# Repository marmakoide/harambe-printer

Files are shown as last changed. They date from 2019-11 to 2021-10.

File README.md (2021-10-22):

# Harambe printer

This repository contains the design of a 3d printer. The printer is very 
similar to a Prusa MK3 with the Bear upgrade. The differences are

* 12mm smooth rods on Z and Y axis for extra rigidity
* 9mm belts on all axes
* Duet2 for control
* Cast aluminium bed with silicon 220V heater
* Self-aligning linear bearings on Z and Y axis

The target I am aiming for is a very reliable, easy to service 3d printer. 

I designed all the 3d printed parts as an exercise to learn 3d modeling and 
mecanical design.

## Authors

* **Alexandre Devert** - *Initial work* - [marmakoide](https://github.com/marmakoide)

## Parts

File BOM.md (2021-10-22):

Bill Of Materials
=================

* Prusa i3 Bear MK3 frame kit
* Filafarm Filabase  218x218 mm 230V/200W heated bed kit
* 2x 12mm smooth rods, length 370 mm
* 2x Nema17 steppers with integrated TR8x8 leadscrew
* 2x TR8x8 leadscrew bronze nuts
* 4x LM12UU linear ball bearings (European specs, 12x22x32 mmm)
* 2x Topball TK12 self-aligning linear ball bearings
* 3x Gates Powergrip® 2GT Toothed Idler 9mm Belt, 20 Teeths
* 1x LRS-350-24, 24V 350 Watts switching power supply
* 1x Duet 2 Wifi control board
* 1x Panel Due touch screen module

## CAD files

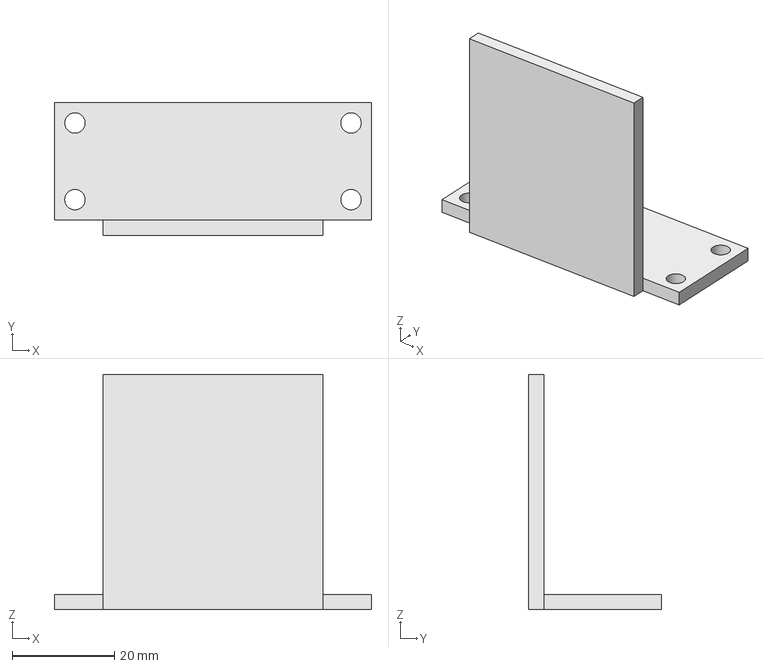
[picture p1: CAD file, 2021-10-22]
parts.FCStd
62.0 x 26.0 x 46.0 mm

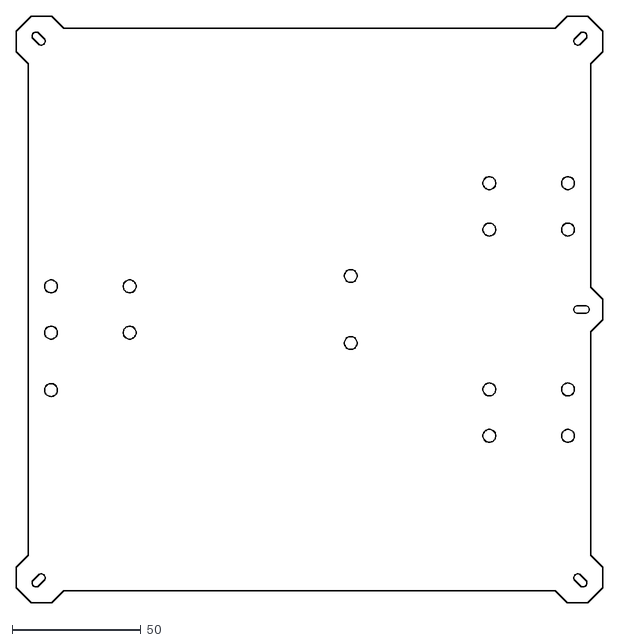
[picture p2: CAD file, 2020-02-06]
parts/dxf/bed-support-plate.dxf
227.3 x 227.3

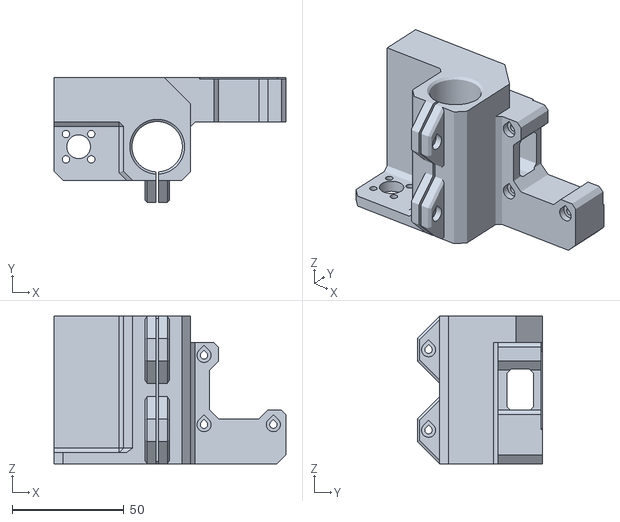
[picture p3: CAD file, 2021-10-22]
parts/stl/x-motor-mount.stl
103.8 x 56.0 x 66.0

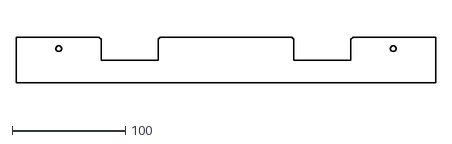
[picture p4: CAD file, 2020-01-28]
parts/dxf/y-axis-fitting-jig-a.dxf
370.0 x 40.0

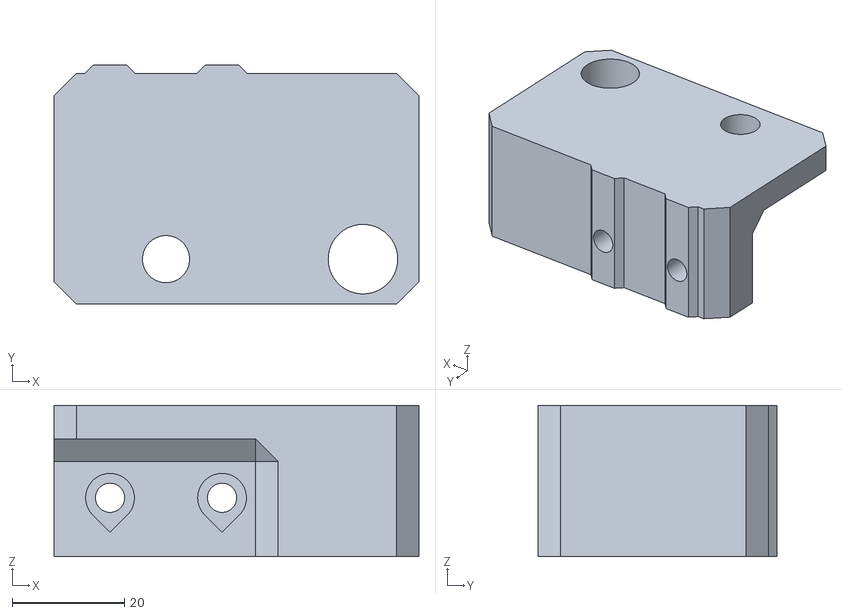
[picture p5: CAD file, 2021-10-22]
parts/stl/z-top.stl
65.2 x 42.7 x 27.0

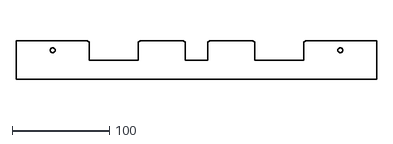
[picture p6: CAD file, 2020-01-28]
parts/dxf/y-axis-fitting-jig-b.dxf
370.0 x 40.0

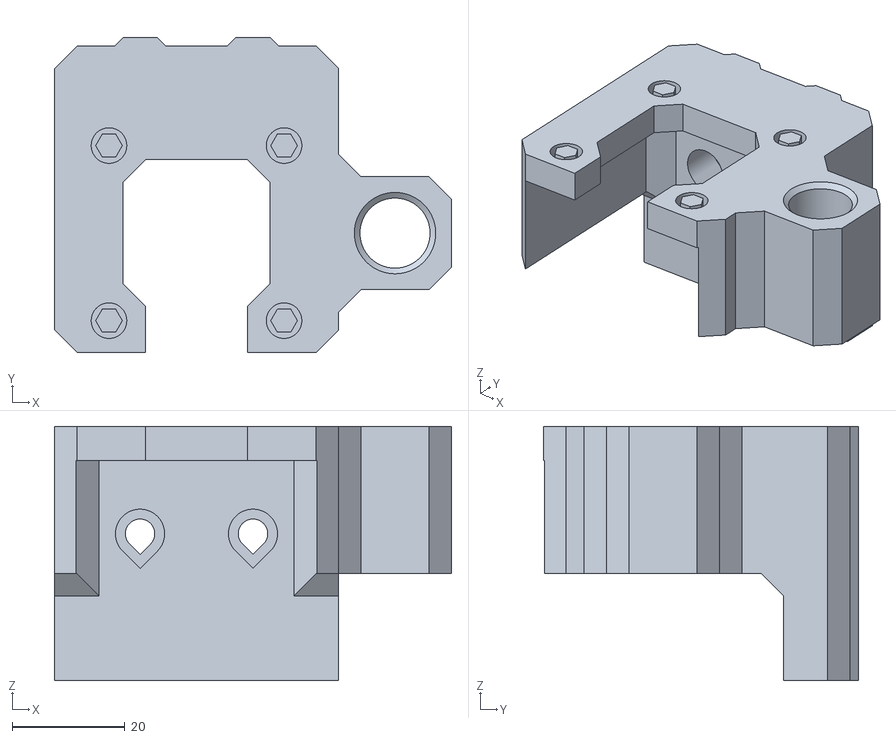
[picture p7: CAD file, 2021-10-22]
parts/stl/z-motor-mount.stl
70.3 x 55.8 x 45.0

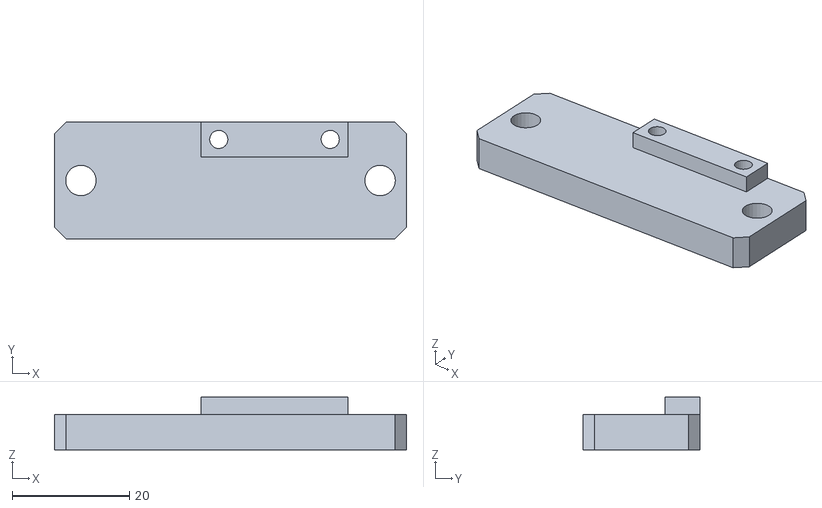
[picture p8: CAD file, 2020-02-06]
parts/stl/y-endstop-support.stl
60.0 x 20.0 x 9.00

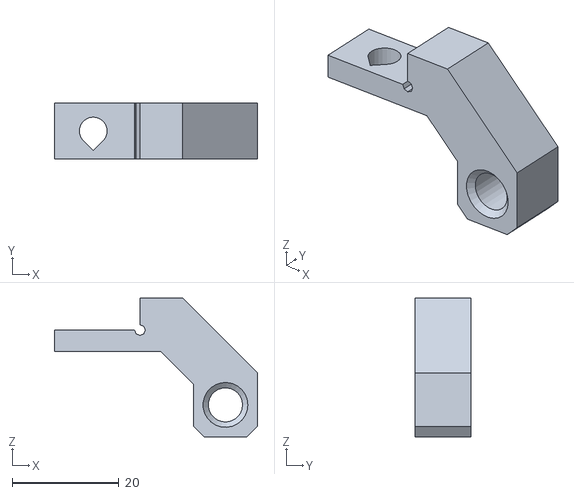
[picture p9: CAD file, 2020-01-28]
parts/stl/y-endstop-hammer-support.stl
38.0 x 10.5 x 26.0

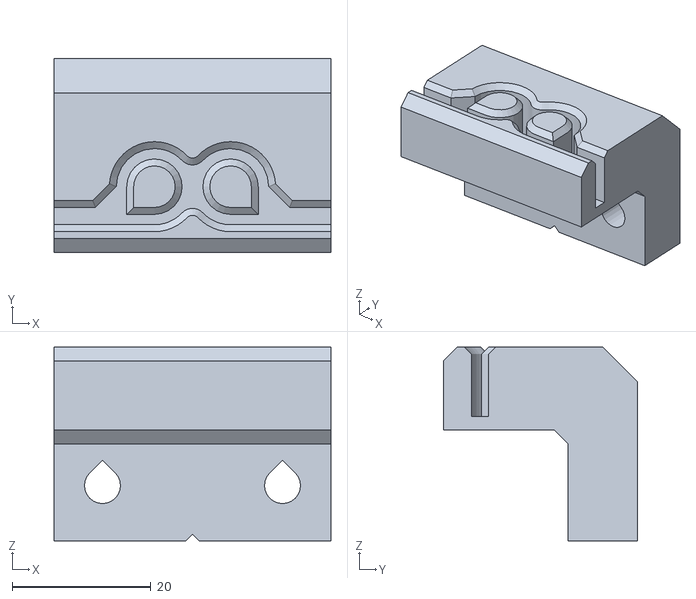
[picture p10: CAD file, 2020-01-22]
parts/stl/y-belt-clamp.stl
40.0 x 28.0 x 28.0

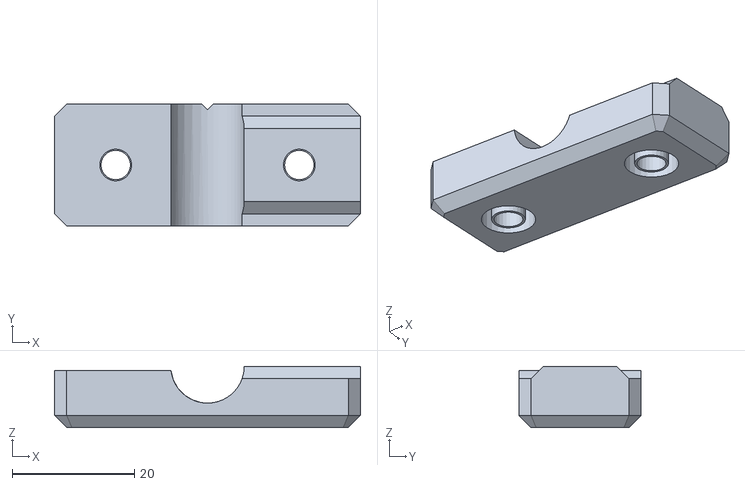
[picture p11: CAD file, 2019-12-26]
parts/stl/y-rod-holder-top.stl
50.0 x 20.0 x 10.0

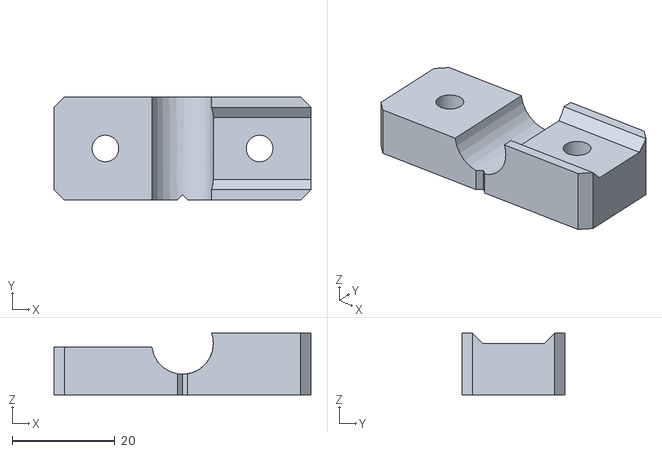
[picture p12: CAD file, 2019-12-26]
parts/stl/y-rod-holder-bottom.stl
50.0 x 20.0 x 12.0

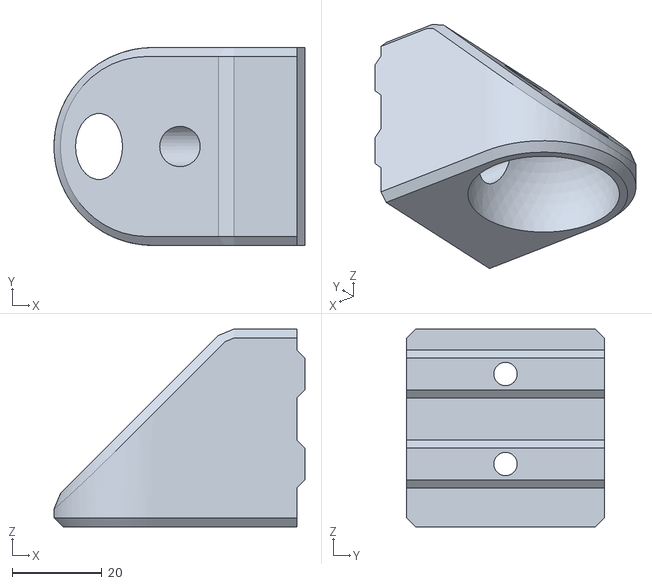
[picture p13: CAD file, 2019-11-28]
parts/stl/foot.stl
55.8 x 44.0 x 44.0

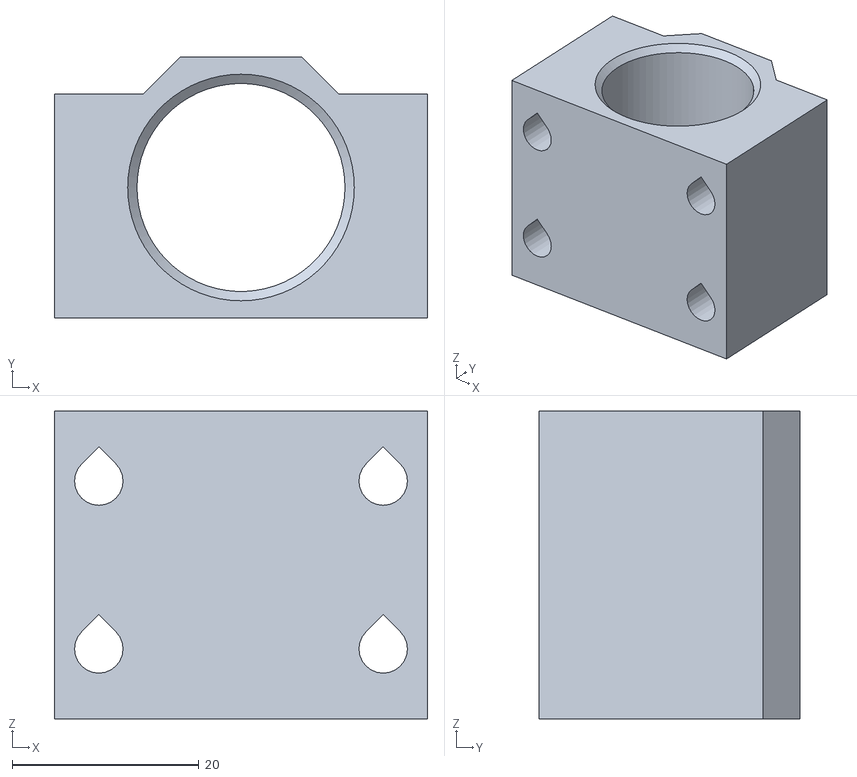
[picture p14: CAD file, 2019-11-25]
parts/stl/y-bearing-holder-type-a.stl
40.0 x 28.0 x 33.0

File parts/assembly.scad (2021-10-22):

include <parts.scad>

X_AXIS_POS = 0 - BED_SIZE / 2;
Y_AXIS_POS = BED_SIZE / 2; //BED_SIZE - 9;
Z_AXIS_POS = 0;



/*
 * Prefab parts
 */

module bmg_extruder() {
  CUBE_SIZE = [42, 33, 33];
  
  HEATBREAK_HEIGHT = 6;
  HEATBREAK_DIAMETER = 5.88;

  
  // Body (upper part is not represented)
  hull() {
    cube(CUBE_SIZE, center = true);
    rotate(90, [0, 0, 1])
      cube(CUBE_SIZE, center = true);
  }
  
  // Bottom part of the heatbreak
  translate([-(CUBE_SIZE[0] + HEATBREAK_HEIGHT) / 2, 4.25, 23 - CUBE_SIZE[0] / 2]) {
    // Bottom part of the heatbreak
    rotate(90, [0, 1, 0])
      kcylinder(HEATBREAK_DIAMETER / 2, HEATBREAK_HEIGHT);
    
    // Heatblock
    translate([-3 - 11.5 / 2 + 6 - 2, 0, 0])
    rotate(90, [0, 1, 0])
    translate([E3D_V6_HEATBLOCK_SIZE_FILAMENT_PATH_OFFSET / 2, 0, 0])
    difference() {
      cube(E3D_V6_HEATBLOCK_SIZE, center = true);
      translate([E3D_V6_HEATBLOCK_SIZE_FILAMENT_PATH_OFFSET - E3D_V6_HEATBLOCK_SIZE[0] / 2, 0, 0])
      kcylinder(3, E3D_V6_HEATBLOCK_SIZE[2] + 2);
    }
  }
}



module nema17(length) {
  CUBE_SIZE = [NEMA_17_SIZE, 33, length];
  
  SHAFT_DIAMETER = 5;
  SHAFT_LENGTH = 24;
  
  FLANGE_DIAMETER = 22;
  FLANGE_HEIGHT = 2;
  
  FIXATION_HOLES_DIAMETER = 3.5;
  FIXATION_HOLES_GAP = 31; 
  FIXATION_HOLES_DEPTH = 15;

  cyl_resolution = 16;
  
  difference() {
    union() {
      // Main body
      color("DarkSlateGray")
        hull() {
          cube(CUBE_SIZE, center = true);
          rotate(90, [0, 0, 1])
            cube(CUBE_SIZE, center = true);
         }

      // Flange
      color(METAL_COLOR)
        translate([0, 0, (CUBE_SIZE[2] / 2) - 1])
          cylinder(h = FLANGE_HEIGHT + 1, d = FLANGE_DIAMETER, center = true, $fn = cyl_resolution);
      
      // Shaft
      color(METAL_COLOR)
        translate([0, 0, (CUBE_SIZE[2] + SHAFT_LENGTH) / 2])
          cylinder(h = SHAFT_LENGTH, d = SHAFT_DIAMETER, center = true, $fn = cyl_resolution);
    }

    // Fixation holes
    //color("DarkSlateGray")
    translate([0, 0, (CUBE_SIZE[2] / 2) - (FIXATION_HOLES_DEPTH / 2) + 1])
      for(i = [-.5, .5], j = [-.5, .5])
        translate([i * FIXATION_HOLES_GAP, j * FIXATION_HOLES_GAP, 0])
          cylinder(h = FIXATION_HOLES_DEPTH + 1, d = FIXATION_HOLES_DIAMETER, center = true, $fn = cyl_resolution);
  }
}




/*
 * Gantry parts
 */

module beam(length) {
  color(BEAM_COLOR)
    vslot_beam(length);
}

module x_beam() {
  rotate(90, [1, 0, 0])
    beam(X_BEAM_SIZE);
}

module y_beam() {
  rotate(90, [0, 0, 1])
    beam(Y_BEAM_SIZE);
}

module z_beam() {
  rotate(90, [0, 0, 1])
  rotate(90, [0, 1, 0])
    beam(Z_BEAM_SIZE);
}

module zx_beam() {
  rotate(90, [1, 0, 0])
    beam(ZX_BEAM_SIZE);
}



/*
 * X axis parts
 */

module x_rod() {
  color(METAL_COLOR)
    rotate(90, [0, 1, 0])
      kcylinder(X_ROD_DIAMETER / 2, X_ROD_LENGTH);
}

module x_bearing_block_() {
  color(PRINTED_PART_COLOR)
    rotate(90, [0, 1, 0])
    rotate(180, [1, 0, 0])
      x_bearing_block();
}

module x_axis_carriage_assembly() {
  // extruder mount plate
  translate([0, X_BEARING_BLOCK_SIZE[1] / 2 + BONDTECH_BMG_MOUNT_SHEET_THICKNESS / 2, 0])
    rotate(180, [0, 1, 0])
    rotate(-90, [1, 0, 0])
    bondtech_bmg_mount();

  // extruder stepper motor
  translate([0, X_BEARING_BLOCK_SIZE[1] / 2 + 43 / 2 + BONDTECH_BMG_MOUNT_SHEET_THICKNESS, 0])
    rotate(180, [0, 1, 0])
    rotate(-90, [0, 1, 0])
      nema17(E_NEMA_17_HEIGHT);
  
  // extruder
  translate([31, X_BEARING_BLOCK_SIZE[1] / 2 + 43 / 2 + BONDTECH_BMG_MOUNT_SHEET_THICKNESS, 0])
    rotate(180, [0, 1, 0])
    rotate(90, [0, 1, 0])  
      bmg_extruder();
  
  // bearing blocks
  translate([-X_BEARING_BLOCK_SIZE[2] / 2, 0, X_ROD_GAP / 2])
    x_bearing_block_();
  
  translate([ X_BEARING_BLOCK_SIZE[2] / 2, 0, X_ROD_GAP / 2])
    x_bearing_block_();
  
  translate([0, 0, -X_ROD_GAP / 2])
    x_bearing_block_();  
}

module x_axis_assembly() {
  // bearing blocks
  translate([X_AXIS_POS, 0, 0])
    x_axis_carriage_assembly();
  
  // X rods
  translate([0, 0, -X_ROD_GAP / 2])
    x_rod();
  
  translate([0, 0, X_ROD_GAP / 2])
    x_rod();  
}



/*
 * Y axis parts
 */

module y_rod() {
  color(METAL_COLOR)
    rotate(90, [1, 0, 0])
      kcylinder(Y_ROD_DIAMETER / 2, Y_ROD_LENGTH);
}

module y_bearing_block_() {
  color(PRINTED_PART_COLOR)
    rotate(90, [1, 0, 0])
    rotate(180, [0, 0, 1])
      render(convexity = 2)
      y_bearing_block();
}

module y_end_stop_support() {
  color(PRINTED_PART_COLOR)
    import("./stl/y-endstop-support.stl", convexity = 3);
}

module y_end_stop_hammer_support() {
  color(PRINTED_PART_COLOR)
    rotate(180, [0, 0, 1])
    import("./stl/y-endstop-hammer-support.stl", convexity = 3);
}

module y_belt_clamp() {
  color(PRINTED_PART_COLOR)
    translate([0, -Y_BELT_CLAMP_SIZE[0] / 2, 0])
    rotate(90, [0, 0, 1])
    rotate(90, [1, 0, 0])
      import("./stl/y-belt-clamp.stl", convexity = 3);
}

module y_motor_mount() {
  color(PRINTED_PART_COLOR)
    rotate(90, [0, 0, 1])
    rotate(90, [1, 0, 0])
      import("./stl/y-motor-mount.stl", convexity = 3);
}

module y_pulley_idler() {
  color(PRINTED_PART_COLOR)
    rotate(180, [0, 1, 0])
    rotate(90, [0, 0, -1])
      import("./stl/y-pulley-idler.stl");
}

module y_pulley_idler_assembly() {
  y_pulley_idler();
  
  translate([0, -18.25, 15 - 21.15])
  rotate(90, [0, 1, 0])
    gates_toothed_idler_9mm();
}

module y_motor_assembly() {
  y_motor_mount();
  
  translate([-(XYZ_NEMA_17_HEIGHT + Y_MOTOR_MOUNT_WIDTH) / 2, NEMA_17_SIZE / 2 + 4, -6.15])
  rotate(90, [0, 1, 0])
    nema17(XYZ_NEMA_17_HEIGHT);
}



module y_axis_assembly() {
  translate([0, -Y_BEAM_SIZE / 2, 0])
    y_motor_assembly();
  
  translate([0,  Y_BEAM_SIZE / 2, 0])
    y_pulley_idler_assembly();
  
  translate([-Y_ROD_GAP / 2 - 50, -Y_BEAM_SIZE / 2 - 10, 0])
    y_end_stop_support();
  
  // Belt
  translate([0, 0, 15 - 21.15])
  rotate(90, [0, 0, 1])
  rotate(90, [1, 0, 0])
    belt(Y_BEAM_SIZE - 40, GATES_TOOTHED_IDLER_OUTER_DIAMETER, 9);

  // Y rods
  translate([0, 0, Y_ROD_DIAMETER / 2 + 4]) {
    translate([-Y_ROD_GAP / 2, 0, 0])
      y_rod();
  
    translate([ Y_ROD_GAP / 2, 0, 0])
      y_rod();
  }  
}



/*
 * Z axis parts
 */

module z_rod() {
  color(METAL_COLOR)
    kcylinder(Z_ROD_DIAMETER / 2, Z_ROD_LENGTH);
}

module z_axis_assembly() {
  // Z rods
  //translate([0, 0, Y_ROD_DIAMETER / 2 + 4]) {
    translate([-Z_ROD_GAP / 2, 0, Z_ROD_LENGTH / 2])
      z_rod();
  
    translate([ Z_ROD_GAP / 2, 0, Z_ROD_LENGTH / 2])
      z_rod();
  //}  
}



/*
 * Bed parts
 */

module bed_support_plate() {
  color("Burlywood")
    linear_extrude(height = BED_SUPPORT_THICKNESS, convexity = 10, center = true)
      bed_support_plate_profile();  
}

module bed_assembly() {
   A = (Y_BEARING_BLOCK_SIZE[1] + Y_BEARING_BLOCK_BEVEL) / 2;
  
  // bed support plate
  translate([0, 0, BED_SUPPORT_THICKNESS / 2 + Y_BEARING_BLOCK_SIZE[1] / 2])
    bed_support_plate();
  
  // belt clamps
  translate([10, 0, 0])
   rotate(180, [0, 0, 1])
    translate([0, 0, 0])
    y_belt_clamp();
  
  // end stop hammer
  translate([-(BED_SIZE / 2 - 16), -(BED_SIZE / 4 - A) - Y_BEARING_BLOCK_SIZE[2] / 2 + Y_ENDSTOP_HAMMER_THICKNESS / 2 + 20, BED_SUPPORT_THICKNESS / 2 + Y_BEARING_BLOCK_SIZE[1] / 2 + BED_SUPPORT_THICKNESS / 2])
    y_end_stop_hammer_support();

  // bearing blocks 
  translate([-Y_ROD_GAP / 2, 0, 0]) {
    translate([0, Y_BEARING_BLOCK_BEVEL / 2, 0])
    rotate(90, [1, 0, 0])
      lm12uue();

    y_bearing_block_();
  }
  
  translate([ Y_ROD_GAP / 2, -(BED_SIZE / 4 - A), 0]) {
    translate([0, Y_BEARING_BLOCK_BEVEL / 2, 0])
    rotate(90, [1, 0, 0])
      lm12uue();
    
    y_bearing_block_();
  }
  
  translate([ Y_ROD_GAP / 2, (BED_SIZE / 4 - A), 0]) {
    translate([0, Y_BEARING_BLOCK_BEVEL / 2, 0])
    rotate(90, [1, 0, 0])
      lm12uue();

    y_bearing_block_();
  }
}



/*
 * Overall assembly
 */

module gantry_assembly() {
  translate([0, -(Y_BEAM_SIZE / 2 + 10), 20])
    x_beam();
  translate([0,  (Y_BEAM_SIZE / 2 + 10), 20])
    x_beam();
  translate([-(Y_BEAM_SIZE / 2), 0, 10])
    y_beam();  
  translate([ (Y_BEAM_SIZE / 2), 0, 10])
    y_beam();
  translate([-(X_BEAM_SIZE / 2 - 20), 0, Z_BEAM_SIZE / 2 + 20]) 
    z_beam();
  translate([ (X_BEAM_SIZE / 2 - 20), 0, Z_BEAM_SIZE / 2 + 20]) 
    z_beam();
  translate([0, 0, Z_BEAM_SIZE])   
    zx_beam();
}



module printer_assembly() {
  // gantry
  gantry_assembly();
  
  // bed
  translate([0, Y_AXIS_POS - BED_SIZE / 2, 40 + 6 + 4])
    bed_assembly();
  
  // x axis
  translate([0, 30, 40 + X_ROD_GAP + 40])
    x_axis_assembly();
  
  // y axis
  translate([0, 0, 40])  
    y_axis_assembly();
  
  // z axis
  translate([0, Z_ROD_DIAMETER / 2 + 10, 20])  
    z_axis_assembly();
}

printer_assembly();

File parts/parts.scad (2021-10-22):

include <utils.scad>



// --- Parameters ------------------------------------------------------------

BEAM_COLOR = "SlateGray";
PRINTED_PART_COLOR = "Orange";
METAL_COLOR = "Gainsboro";
BELT_COLOR = "Black";

X_BEAM_SIZE  = 370;
Y_BEAM_SIZE  = 331;
Z_BEAM_SIZE  = 359; 
ZX_BEAM_SIZE = 290; 

// Nema17 stepper motor specs
NEMA_17_SIZE = 42.3;
XYZ_NEMA_17_HEIGHT = 39.8;
E_NEMA_17_HEIGHT = 23;

// Gates pulleys specs
GATES_TOOTHED_IDLER_OUTER_DIAMETER = 15;

// E3D V6 heatblock
E3D_V6_HEATBLOCK_SIZE = [23, 16, 11.5];
E3D_V6_HEATBLOCK_SIZE_FILAMENT_PATH_OFFSET = 8;

// LM8UUE bearing specs
LM8UUE_L = 25;
LM8UUE_D = 16;

// LM12UUE bearing specs
LM12UUE_L = 32;
LM12UUE_D = 22;

// Extruder elements
BONDTECH_BMG_MOUNT_PLATE_SIZE = [23, 62];
BONDTECH_BMG_MOUNT_SHEET_THICKNESS = 3;
BONDTECH_BMG_MOUNT_HOLE_DIAMETER = 4;

// X axis design
X_ROD_DIAMETER = 8;
X_ROD_LENGTH = 500;
X_ROD_GAP = 50;

// Y axis design
Y_ROD_DIAMETER = 12;
Y_ROD_LENGTH = Y_BEAM_SIZE + 40;
Y_ROD_GAP = 170;

// Z axis design
Z_ROD_DIAMETER = 12;
Z_ROD_LENGTH = Z_BEAM_SIZE;
Z_ROD_GAP = X_BEAM_SIZE - 20; 

// Y rod holders
Y_ROD_HOLDER_SIZE = [50, 40, 2 * 4 + Y_ROD_DIAMETER];

// Y belt clamp
Y_BELT_CLAMP_SIZE = [40, 28, 28];
Y_BELT_CLAMP_FIXATION_HOLE_GAP = 26;

// Y end stop hammer
Y_ENDSTOP_HAMMER_THICKNESS = 10.5;

// Y motor mount
Y_MOTOR_MOUNT_WIDTH = 23;
Y_MOTOR_MOUNT_MOTOR_BEAM_GAP = 4;

// X bearing blocks
X_BEARING_LENGTH = LM8UUE_L;
X_BEARING_DIAMETER = LM8UUE_D;
X_BEARING_BLOCK_BEVEL = 1;
X_BEARING_BLOCK_SIZE = [34, 22, X_BEARING_LENGTH + X_BEARING_BLOCK_BEVEL];
X_BEARING_BLOCK_FIXATION_HOLE_GAP_X = 24;
X_BEARING_BLOCK_FIXATION_HOLE_GAP_Y = 13;

// Y bearing blocks
Y_BEARING_LENGTH = LM12UUE_L;
Y_BEARING_DIAMETER = LM12UUE_D;
Y_BEARING_BLOCK_BEVEL = 1;
Y_BEARING_BLOCK_SIZE = [40, 28, Y_BEARING_LENGTH + Y_BEARING_BLOCK_BEVEL];
Y_BEARING_BLOCK_FIXATION_HOLE_GAP_X = 30.5;
Y_BEARING_BLOCK_FIXATION_HOLE_GAP_Y = 18;

// Y axis fitting jigs 
Y_AXIS_FITTING_JIG_TOLERANCE = .2;
Y_AXIS_FITTING_JIG_CHAMFER = 2;

BED_SIZE = 218;

BED_SUPPORT_ADJUSTEMENT_SCREW_GAP = 5;
BED_SUPPORT_ADJUSTEMENT_SCREW_SLOT_LENGTH = 3;
BED_SUPPORT_THICKNESS = 6;

M3_LASER_CUT_HOLE_DIAMETER = 3.;

M4_LASER_CUT_HOLE_DIAMETER = 4.;

M5_3D_PRINT_HOLE_DIAMETER = 5.2;
M5_LASER_CUT_HOLE_DIAMETER = 5.;


// --- Utilities -------------------------------------------------------------

// Circumradius of an octagon with size 1
octagon_circumradius = (sqrt(4 + 2 * sqrt(2))) / 2;

module k_negative_rectangle(size, chamfer) {
  square(size, center = true);
  polygon([
            [-(size[0] / 2 + chamfer), size[1] / 2],
            [  size[0] / 2 + chamfer,  size[1] / 2],
            [  size[0] / 2,            size[1] / 2 - chamfer],
            [ -size[0] / 2,            size[1] / 2 - chamfer]
          ], convexity = 1);
}



// --- Commonly used elements -------------------------------------------------

module m4_teardrop_3d_print() {
  kteardrop(M4_LASER_CUT_HOLE_DIAMETER / 2);
}

module m5_teardrop_3d_print() {
  kteardrop(M5_LASER_CUT_HOLE_DIAMETER / 2);
}

module m3_circle_laser_cut() {
  kcircle(M3_LASER_CUT_HOLE_DIAMETER / 2);
}

module m5_circle_laser_cut() {
  kcircle(M5_LASER_CUT_HOLE_DIAMETER / 2);
}



// --- GT2 belt ----------------------------------------------------------------------------------

module belt(length, diameter, width) {
  THICKNESS = 0.63;
  
  color(BELT_COLOR)
    linear_extrude(height = width, center = true)
      difference() {
        kcapsule(length, diameter / 2 + THICKNESS);
        kcapsule(length, diameter / 2);
      }
}



// --- Linear bearings ---------------------------------------------------------------------------

module lm12uue() {
  color(METAL_COLOR)
    difference() {
      kcylinder(LM12UUE_D / 2, LM12UUE_L);
      kcylinder(6, LM12UUE_L + 2);
    }
}



module lm8uue() {
  color(METAL_COLOR)
    difference() {
      kcylinder(LM8UUE_D / 2, LM8UUE_L);
      kcylinder(4, LM8UUE_L + 2);
    }
}



// --- Gates pulley idler for 9mm 2GT belts ------------------------------------------------------

module gates_toothed_idler_9mm() {
  HOLE_DIAMETER = 5;
  INNER_DIAMETER = 12.22;
  OUTER_DIAMETER = GATES_TOOTHED_IDLER_OUTER_DIAMETER;
  LENGTH = 14;
  BORDER_SIZE = 1.5;
  
  color(METAL_COLOR) {
    difference() {
      union() {
        kcylinder(INNER_DIAMETER / 2, LENGTH);
      
        translate([0, 0, (LENGTH - BORDER_SIZE) / 2])
          kcylinder(OUTER_DIAMETER / 2, BORDER_SIZE);
        
        translate([0, 0, -(LENGTH - BORDER_SIZE) / 2])
          kcylinder(OUTER_DIAMETER / 2, BORDER_SIZE);
      }
      
      kcylinder(HOLE_DIAMETER / 2, 16.);      
    }
  }
}



// --- Bondtech BMG extruder mount ---------------------------------------------------------------

module bondtech_bmg_mount() {
  color(METAL_COLOR) {
    linear_extrude(height = BONDTECH_BMG_MOUNT_SHEET_THICKNESS, center = true) {
      difference() {
        square(BONDTECH_BMG_MOUNT_PLATE_SIZE, center = true);
        translate([-15 / 2, -55 / 2])
          kcircle(BONDTECH_BMG_MOUNT_HOLE_DIAMETER / 2);
        translate([ 15 / 2, -55 / 2])
          kcircle(BONDTECH_BMG_MOUNT_HOLE_DIAMETER / 2);
        translate([-15 / 2,  55 / 2])
          kcircle(BONDTECH_BMG_MOUNT_HOLE_DIAMETER / 2);
        translate([ 15 / 2,  55 / 2])
          kcircle(BONDTECH_BMG_MOUNT_HOLE_DIAMETER / 2);
      }
    }
    
    translate([-(BONDTECH_BMG_MOUNT_PLATE_SIZE[0] + BONDTECH_BMG_MOUNT_SHEET_THICKNESS) / 2, 0, 43 / 2 + BONDTECH_BMG_MOUNT_SHEET_THICKNESS])
    rotate(90, [1, 0, 0])
    rotate(90, [0, 1, 0])
    linear_extrude(height = BONDTECH_BMG_MOUNT_SHEET_THICKNESS, center = true) {
      difference() {
        translate([0, -BONDTECH_BMG_MOUNT_SHEET_THICKNESS])
          square([43, 46], center = true);
        
        translate([0, -BONDTECH_BMG_MOUNT_SHEET_THICKNESS / 2]) {
          kcircle(23 / 2);
        
          translate([-31 / 2, -31 / 2])
            kcircle(BONDTECH_BMG_MOUNT_HOLE_DIAMETER / 2);
          translate([ 31 / 2, -31 / 2])
            kcircle(BONDTECH_BMG_MOUNT_HOLE_DIAMETER / 2);
          translate([-31 / 2,  31 / 2])
            kcircle(BONDTECH_BMG_MOUNT_HOLE_DIAMETER / 2);
          translate([ 31 / 2,  31 / 2])
            kcircle(BONDTECH_BMG_MOUNT_HOLE_DIAMETER / 2);
        }
      }
    }
  }
}



// --- X bearing block --------------------------------------------------------

module x_bearing_block() {
  FLAT_HEIGHT = 3;
  A = X_BEARING_BLOCK_SIZE[0] - X_BEARING_BLOCK_FIXATION_HOLE_GAP_X;
  
  BEARING_BLOCK_FIXATION_HOLE_POS_LIST = [
    [-X_BEARING_BLOCK_FIXATION_HOLE_GAP_X, 0, -X_BEARING_BLOCK_FIXATION_HOLE_GAP_Y],
    [ X_BEARING_BLOCK_FIXATION_HOLE_GAP_X, 0, -X_BEARING_BLOCK_FIXATION_HOLE_GAP_Y],
    [-X_BEARING_BLOCK_FIXATION_HOLE_GAP_X, 0,  X_BEARING_BLOCK_FIXATION_HOLE_GAP_Y],
    [ X_BEARING_BLOCK_FIXATION_HOLE_GAP_X, 0,  X_BEARING_BLOCK_FIXATION_HOLE_GAP_Y]
  ] / 2;
  
  difference() {
    // Main shape
    linear_extrude(height = X_BEARING_BLOCK_SIZE[2], convexity = 2, center = true)
      difference() {
        // Bearing hole profile
        polygon([
          [ X_BEARING_BLOCK_SIZE[0] / 2, -X_BEARING_BLOCK_SIZE[1] / 2],
          [ X_BEARING_BLOCK_SIZE[0] / 2,  X_BEARING_BLOCK_SIZE[1] / 2 - FLAT_HEIGHT],
          [ X_BEARING_BLOCK_SIZE[0] / 2 - A,  X_BEARING_BLOCK_SIZE[1] / 2 - FLAT_HEIGHT],
          [ X_BEARING_BLOCK_SIZE[0] / 2 - A - FLAT_HEIGHT,  X_BEARING_BLOCK_SIZE[1] / 2],
          [-X_BEARING_BLOCK_SIZE[0] / 2 + A + FLAT_HEIGHT,  X_BEARING_BLOCK_SIZE[1] / 2], 
          [-X_BEARING_BLOCK_SIZE[0] / 2 + A,  X_BEARING_BLOCK_SIZE[1] / 2 - FLAT_HEIGHT],
          [-X_BEARING_BLOCK_SIZE[0] / 2,  X_BEARING_BLOCK_SIZE[1] / 2 - FLAT_HEIGHT],
          [-X_BEARING_BLOCK_SIZE[0] / 2, -X_BEARING_BLOCK_SIZE[1] / 2],        
        ], convexity = 1);
      
        // Bearing hole
        kcircle(X_BEARING_DIAMETER / 2);
      }
      
    // Fixation holes
    for(pos = BEARING_BLOCK_FIXATION_HOLE_POS_LIST)
      translate(pos)
        rotate(90, [1, 0, 0])
          linear_extrude(height = 2 * X_BEARING_BLOCK_SIZE[1], convexity = 1, center = true)
            rotate(90)
              m4_teardrop_3d_print();
    
    // Bearing hole bevel
    translate([0, 0, X_BEARING_BLOCK_SIZE[2] / 2])
      round_hole_bevel(X_BEARING_DIAMETER / 2, X_BEARING_BLOCK_BEVEL, [0, 0, 1]);    
  }  
}

//x_bearing_block();



// --- Y bearing block --------------------------------------------------------
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

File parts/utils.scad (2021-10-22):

CHORD_LEN = .4; // Length of segments used to approximate curves


function mirror_x(U) =
  [-U[0], U[1]];



/*
 * Euclidean norm and distance
 */
 
function norm2(v) =
  sqrt(v * v);

function dist(A, B) =
	norm2([B[0] - A[0], B[1] - A[1]]);
  
  

/*
 * Rotate an object so that U aligns to V
 */
 
module align_to_axis(U, V) {
  rotate(acos(U * V), cross(U, V))
    children(0);
}



/*
 * Produce n evenly spaced values in [a, b] interval
 */
 
function linspace(a, b, n) =
  [ for (_i = [ 0 : n - 1 ] ) a + _i * (b - a) / (n - 1) ];
  
function linspace_noend(a, b, n) =
  [ for (_i = [ 0 : n - 1 ] ) a + _i * (b - a) / n ];




function chord_len_2_angle(radius, chord_len) =
  acos(1. - (chord_len * chord_len) / (2 * radius * radius));
	
function chord_len_2_step_count(chord_len, radius, angle) = 
  ceil(angle / chord_len_2_angle(radius, chord_len));

module kcircle_sector(radius, angle) {
	n = chord_len_2_step_count(CHORD_LEN, radius, angle);
	polygon(concat([[0,0]], radius * [for(angle = linspace(0, angle, n)) [cos(angle), sin(angle)]]), convexity = 1);
}



/*
 * Origin centered circle
 */

module kcircle(radius) {
	n = chord_len_2_step_count(CHORD_LEN, radius, 360);
	polygon(radius * [for(alpha = linspace_noend(0, 360, n)) [cos(alpha), sin(alpha)]], convexity = 1);	
}



/*
 * Origin centered cylinder, along Z axis
 */

module kcylinder(radius, height) {
	linear_extrude(height = height, center = true, convexity = 1)
		kcircle(radius);
}



/*
 * Origin centered cone, along Z axis
 */

module kcone(radius, height) {
  linear_extrude(height = height, center = true, scale = 0, convexity = 1)
    kcircle(radius);
}



/*
 * Origin centered capsule, along Z axis
 */


module kcapsule(length, radius) {
	n = chord_len_2_step_count(CHORD_LEN, radius, 180);

	hi = [for(alpha = linspace( -90,  90., n)) [radius * cos(alpha) + length / 2, radius * sin(alpha)]];
	lo = [for(alpha = linspace(  90,  270, n)) [radius * cos(alpha) - length / 2, radius * sin(alpha)]];

	polygon(concat(hi, lo), convexity = 1);
}

module kcapsule_from_end_points(A, B, radius) {
	length = dist(A, B);
	U = [B[0] - A[0], B[1] - A[1]] / length;
	
	translate(.5 * [A[0] + B[0], A[1] + B[1]])
		rotate(atan2(U[1], U[0]))
			kcapsule(length, radius);
}



/*
 * Origin centered 'teardrop'
 */

module kteardrop(radius) {
  angle = 270;
	n = chord_len_2_step_count(CHORD_LEN, radius, angle);
  rotate(45)
    polygon(concat([[radius,-radius]], radius * [for(angle = linspace(0, angle, n)) [cos(angle), sin(angle)]]), convexity = 1);
}



/*
 * Unit octahedron
 */
 
module octahedron() {
  X = [1, 0, 0];
  Y = [0, 1, 0];
  Z = [0, 0, 1];
  
  polyhedron(
    points = [X, Y, Z, -X, -Y, -Z],
    faces = [
      [1, 0, 2],
      [0, 1, 5],
      [0, 4, 2],
      [4, 0, 5],
      [4, 3, 2],
      [3, 4, 5],
      [3, 1, 2],
      [1, 3, 5]  
    ],
    convexity = 2);
}



/*
 * Box centered on the origin, with a bevel on each edges
 */

module bevel_box(size, bevel) {
  s = (size[0] + size[1] + size[2]) / 2 - 2 * bevel;
  sz = (size[0] + size[1] - 2 * bevel) / sqrt(2);
  sx = (size[1] + size[2] - 2 * bevel) / sqrt(2);
  sy = (size[2] + size[0] - 2 * bevel) / sqrt(2);
  
  intersection() {
    cube(size, center = true);
    rotate(45, [0, 0, 1])
      cube([sz, sz, size[2]], center = true);
    rotate(45, [1, 0, 0])
      cube([size[0], sx, sx], center = true);
    rotate(45, [0, 1, 0])
      cube([sy, size[1], sy], center = true);    
    scale(s)
      octahedron();
  }
}



/*
 * Generate a bevel for a round hole
 */

module round_hole_bevel(radius, bevel, axis) {
  align_to_axis([0, 0, 1], axis) 
    linear_extrude(height = 2 * bevel, center = true, scale = (radius + 2 * bevel) / radius, convexity = 1)
      kcircle(radius);  
}

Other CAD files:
parts/stl/y-pulley-idler.stl
parts/stl/y-motor-mount.stl

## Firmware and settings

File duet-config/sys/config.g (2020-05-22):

; Configuration file for Duet WiFi (firmware version 3)
; executed by the firmware on start-up
;
; generated by RepRapFirmware Configuration Tool v2.1.8 on Sat May 16 2020 23:03:57 GMT+0800 (China Standard Time)

; General preferences
G90                                            ; send absolute coordinates...
M83                                            ; ...but relative extruder moves
M550 P"harambe"                                ; set printer name

; Network
M552 S1                                        ; enable network
M586 P0 S1                                     ; enable HTTP
M586 P1 S0                                     ; disable FTP
M586 P2 S0                                     ; disable Telnet

; Drives
M569 P0 S1                                     ; physical drive 0 goes forwards
M569 P1 S1                                     ; physical drive 1 goes forwards
M569 P2 S1                                     ; physical drive 2 goes forwards
M569 P3 S1                                     ; physical drive 3 goes forwards
M584 X0 Y1 Z2 E3                               ; set drive mapping
M350 X16 Y16 Z16 E16 I1                        ; configure microstepping with interpolation
M92 X80.00 Y80.00 Z4000.00 E420.00             ; set steps per mm
M566 X900.00 Y900.00 Z12.00 E120.00            ; set maximum instantaneous speed changes (mm/min)
M203 X6000.00 Y6000.00 Z180.00 E1200.00        ; set maximum speeds (mm/min)
M201 X500.00 Y500.00 Z20.00 E250.00            ; set accelerations (mm/s^2)
M906 X800 Y800 Z800 E800 I30                   ; set motor currents (mA) and motor idle factor in per cent
M84 S30                                        ; Set idle timeout

; Axis Limits
M208 X0 Y0 Z0 S1                               ; set axis minima
M208 X218 Y218 Z200 S0                         ; set axis maxima

; Endstops
M574 X1 S1 P"null"                             ; configure active-high endstop for low end on X via pin null
M574 Y1 S1 P"!ystop"                           ; configure active-low endstop for low end on Y via pin ystop

; Z-Probe
M558 P0 H5 F120 T6000                          ; disable Z probe but set dive height, probe speed and travel speed
M557 X9:209 Y9:209 S20                         ; define mesh grid

; Heaters
M308 S0 P"bedtemp" Y"thermistor" T100000 B4138 ; configure sensor 0 as thermistor on pin bedtemp
M950 H0 C"bedheat" T0                          ; create bed heater output on bedheat and map it to sensor 0
M143 H0 S120                                   ; set temperature limit for heater 0 to 120C
M307 H0 B0 S1.00                               ; disable bang-bang mode for the bed heater and set PWM limit
M140 H0                                        ; map heated bed to heater 0
M308 S1 P"spi.cs1" Y"rtd-max31865"             ; configure sensor 1 as PT100 thermistor on pin spi.cs1 (Duet PT100 daughterboard)
M950 H1 C"e0heat" T1                           ; create nozzle heater output on e0heat and map it to sensor 1
M143 H1 S280                                   ; set temperature limit for heater 1 to 280C
M307 H1 B0 S1.00                               ; disable bang-bang mode for heater  and set PWM limit

; Fans
M950 F0 C"fan0" Q500                           ; create fan 0 on pin fan0 and set its frequency
M106 P0 S0 H-1                                 ; set fan 0 value. Thermostatic control is turned off
M950 F1 C"fan1" Q500                           ; create fan 1 on pin fan1 and set its frequency
M106 P1 S1 H1 T45                              ; set fan 1 value. Thermostatic control is turned on

; Tools
M563 P0 D0 H1 F0                               ; define tool 0
G10 P0 X0 Y0 Z0                                ; set tool 0 axis offsets
G10 P0 R0 S0                                   ; set initial tool 0 active and standby temperatures to 0C

; Custom settings are not defined

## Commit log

2019-11-18 Added y-pulley-idler and y-rod-holder parts
    [y-pulley-idler.stl, y-rod-holder-bottom.stl, y-rod-holder-top.stl]
2019-11-18 oriented y-pulley-idler in printing position
    [y-pulley-idler.stl]
2019-11-18 oriented y-rod-holder-top in printing position
    [y-rod-holder-top.stl]
2019-11-18 Created BOM.md
2019-11-19 added y-motor-mount
    [y-motor-mount.stl]
2019-11-21 Y pulley idler revision : thicker walls, fixation screw too low on vslot, small notch to help placement on vslot
    [y-pulley-idler.stl]
2019-11-25 added y-bearing-holder-type-a
    [y-bearing-holder-type-a.stl]
2019-11-28 Added foot part
    [foot.stl]
2019-12-11 Added z pulley idler part
    [z-pulley-idler.stl, z-pulley-idler_supported.stl]
2019-12-11 Updated BOM.md
2019-12-13 Added y-belt-clamp
    [y-belt-clamp.stl]
2019-12-13 y-belt-clamp fixation holes uses less matter
    [y-belt-clamp.stl]
2019-12-26 Added bed support plate
    [bed-support-plate.dxf]
2019-12-26 added parts.scad
    [parts.scad]
2019-12-26 y-bearing-block defined in openscad, bed support plate uses M3 screws to attach bed plate
    [bed-support-plate.dxf, parts.scad]
2019-12-26 revised y belt clamp, all dimensions corrected
    [y-belt-clamp.stl]
2019-12-26 y rod holders have a notch to help positioning, and screws heads are sinked into the holders, saves 5 mm
    [y-rod-holder-bottom.stl, y-rod-holder-top.stl]
2020-01-01 Added fitting jigs to assist y axis construction
    [parts.scad, y-axis-fitting-jig-a.dxf, y-axis-fitting-jig-b.dxf]
2020-01-01 Added svg version y axis svg
    [bed-support-plate.dxf, parts.scad]
2020-01-22 Much more compact y belt clamp, bed can now move freely
    [bed-support-plate.dxf, y-belt-clamp.stl]
2020-01-22 added assembly simulation
    [assembly.scad]
2020-01-25 Slight shift of y-belt-clamp on the bed support, to align the y belt
    [assembly.scad, parts.scad]
2020-01-28 y endstop hammer
    [assembly.scad, parts.scad, y-axis-fitting-jig-a.dxf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]
2020-01-28 renamed y-end-stop y-endstop
    [y-endstop-hammer-support.stl]
2020-01-28 updated SVG and DXF for bed support plate
    [bed-support-plate.dxf, parts.scad]
2020-02-06 y axis fully functional
    [assembly.scad, bed-support-plate.dxf, parts.scad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]
2020-02-06 added configuration for duet
    [bed.g, config.g, homeall.g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]
2020-05-22 Updated sys/config.g for compliance with Duet 2 firmware 3.1, configuration for PT100 thermistor
    [config.g]
2020-05-26 Added belts, extruder and full gantry definition
    [assembly.scad, parts.scad]
2020-05-26 Added models for the linear bearings
    [assembly.scad, parts.scad]
2021-10-22 Completly forgot WTF I did
    [assembly.scad, bed.g, homeall.g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]
2021-10-22 Added parts for Z axis
    [z-motor-mount.stl, z-pulley-idler.stl, z-pulley-idler_supported.stl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]
2021-10-22 Added X motor mount
    [x-motor-mount.stl]
2021-10-22 Added FreeCAD project that will contain all parts
    [parts.FCStd]
